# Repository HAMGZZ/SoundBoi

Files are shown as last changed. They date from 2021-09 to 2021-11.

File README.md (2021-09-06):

# SoundBoi
SoundBoi is the codename for a porject which is intended to use with the [BLAT!](https://github.com/hamgzz/BLAT) module for the holden commodored OEM bimodel exhaust. However, it can be extended for use with other cars and valved mufflers. This project originally started when I still had my Holden Barina and wanted an automatic exhaust valve. Over time from trying to write my own CAN transceiver using the teensy line of transceivers and using dodgy rip-off ELM327s with ESP32s, I finally bit the bullet and invested in a few actual ELM327 chips... This is where SoundBoi comes in. SoundBoi is a complete custom solution using the ELM327 chip and an atTiny1614 to communicate with BLAT!. BLAT! is the module the creates the specific PWM and voltages needed to control the OEM Holden mufflers... And yes, all this could be built into one board, but BLAT! came before SoundBoi...

The board follow's a specific set of rules which can be found in the source code.

## Rules
The SoundBoi uses 4 states and a set of rules it follows to determine if the valves should be oppened or closed.
The valve will be open for the first 5 seconds since the car's startup.

### Rules 1 (Default state)
The valve will open if:
 - Speed < 90 AND:
 	- RPM       > 3000
 	- Load      > 50%
 	- Throttle  > 50%
 - Speed > 90 AND:
	- RPM       > 4000
	- Load      > 70%
	- Throttle  > 80%
 - Speed < 5 AND engine is up to temperature.

### Rules 2
The valve will open if:
 - Speed < 90 AND:
	- RPM       > 1900
	- Load      > 30%
	- Throttle  > 30%
 - Speed > 90:
	- Revert back to Rules set 1.
 - Speed < 15 AND engine is up to temperature.

### Rules 3
The valve is always open.

### Rules 4
The valve is always closed.

## PCB

The PCB is meant to be attached to the BLAT! module back-to-back. This is to keep the boards small and modular. The SoundBoi PCB takes it's 5V from the Pololu [regulator](https://www.pololu.com/product/2843) and reads the battery voltage from the 12v coming from the relay on the BLAT! module. Because of the ignition relay, there is no need for low power cutoff on the SoundBoi module, but it might come in future revisions....

### Schematic

<object data="PCB/SoundBoi/SoundBoi.pdf" type="application/pdf" width="700px" height="700px">
    <embed src="PCB/SoundBoi/SoundBoi.pdf">
        <p>This browser does not support PDFs. Please download the PDF to view it: <a href="PCB/SoundBoi/SoundBoi.pdf">Download PDF</a>.</p>
    </embed>
</object>

### 3D Models
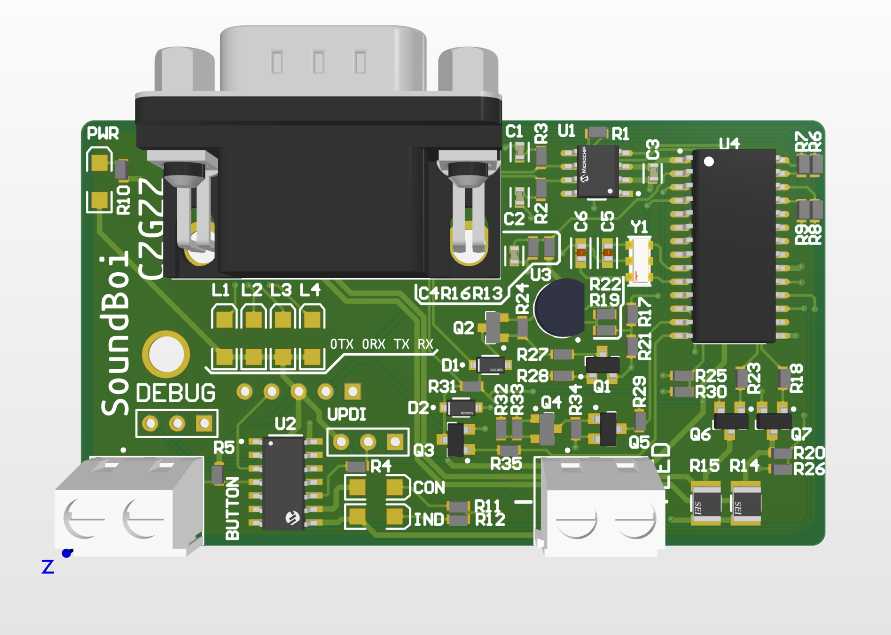
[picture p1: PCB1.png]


### BOM

|Description |Designator |Value  |Manufacturer Part Number 1|Footprint |Quantity|
|---|---|---|---|---|---|
|Female Header, Pitch 5 mm, 1 x 2 Position, Height 10 mm, Tail Length 3.5 mm, Rohs, Bulk |BUTTON, LED | |282836-2 |TECO-282836-2_V |2 |
|CAP CER 560PF 50V X7R 0603 |C1, C2 |560 pF |C0603C561K5RACTU |FP-C0603C-CF-MFG |2 |
|CAP CER 0.1UF 50V X7R 0603 |C3, C4 |0.10 uF|C0603C104K5RACTU |FP-C0603C-CF-MFG |2 |
|Multilayer Ceramic Capacitors 27pF  5% 50V NP0 SMD 0603 |C5, C6 | |C1608NP01H270J080AA |FP-C1608-080-0_1-IPC_A|2 |
|Typical RED, GREEN, YELLOW, AMBER GaAs LED |CON, IND, L1, L2, L3, L4, PWR | | |3.2X1.6X1.1 |7 |
|DIODE GEN PURP 100V 150MA SOD123 |D1, D2 |2pF |1N4148W-13-F |FP-SOD123-MFG |2 |
|Header, 3-Pin |DEBUG, UPDI | | |HDR1X3 |2 |
|Male PCB Connector with Hex Screw WR-DSUB, 10.30 mm, Angled, 9 pins |J1 | |618009231421 |618009231421 |1 |
|Header, 5-Pin |P2 | | |HDR1X5 |1 |
|NPN General Purpose Amplifier, 40 V, 0.2 A, -55 to 150 degC, 3-Pin SOT23, RoHS, Tape and Reel|Q1, Q3, Q5, Q6, Q7 | |MMBT3904 |FAIR-SOT23-3_V |5 |
|General Purpose Transistor, PNP Silicon, 3-Pin SOT-23, Pb-Free, Tape and Reel |Q2, Q4 | |MMBT3906LT1G |ONSC-SOT-23-3-318-08_V|2 |
|Resistor |R1, R4, R27, R28, R29, R35 |4.7K | |J1-0603 |6 |
|Resistor |R2, R3 |100 | |J1-0603 |2 |
|Resistor |R5, R16, R24, R30, R32, R34 |10K | |J1-0603 |6 |
|Resistor |R6, R7, R8, R9, R10, R11, R12, R19, R22|470 | |J1-0603 |9 |
|Resistor |R13, R20, R33 |47K | |J1-0603 |3 |
|510O  5% 0.5W 1210 Thick Film Chip Resistor AEC-Q200 compliant |R14, R15 | |RMCF1210JT510R |FP-RMCF1210-MFG |2 |
|Resistor |R17, R18, R23 |2.2K | |J1-0603 |3 |
|Resistor |R21 |1.8K | |J1-0603 |1 |
|Resistor |R25, R31 |22K | |J1-0603 |2 |
|Resistor |R26 |33K | |J1-0603 |1 |
|IC TRANSCEIVER HALF 1/1 8SOIC |U1 | |MCP2551T-I/SN |FP-C04-057-SN-IPC_B |1 |
|IC MCU 8BIT 16KB FLASH 14SOIC |U2 | |ATTINY1614-SSFR |FP-C04-065-D3X-MFG |1 |
|3-Terminal Adjustable Regulator, 3-pin TO-92 |U3 | |LM317LZG |Z03A |1 |
| |U4 | | |SOIC28 |1 |
|CERAMIC RES 4.0000MHZ 15PF SMD |Y1 | |CSTCR4M00G53-R0 |FP-CSTCR4M00G53-R0-MFG|1 |

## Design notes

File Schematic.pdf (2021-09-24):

# Indicator LEDs

# CAN BUS Transciever

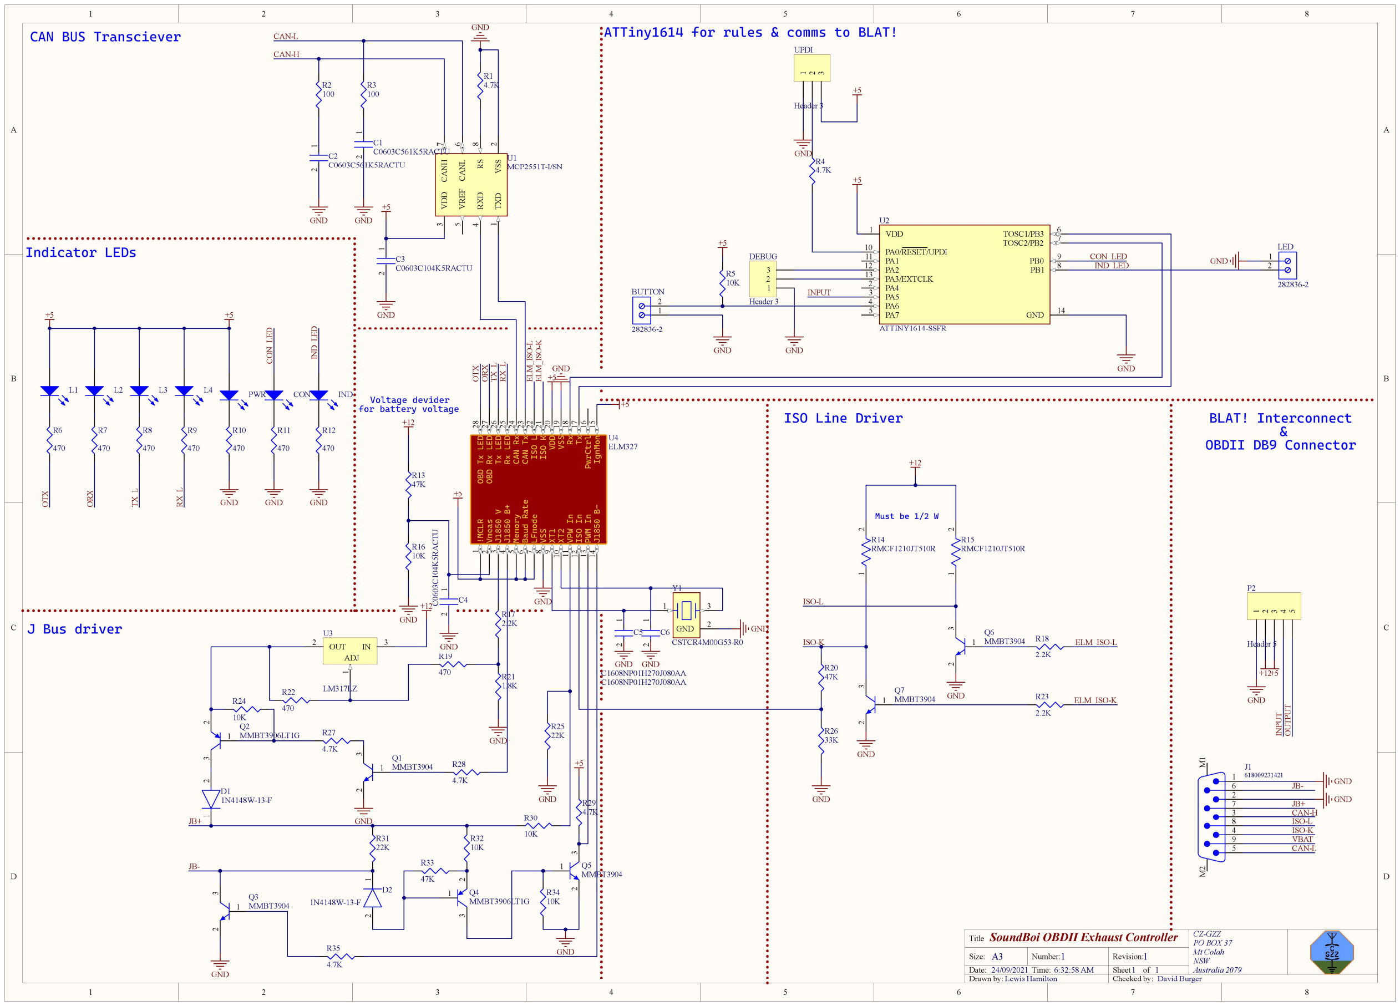
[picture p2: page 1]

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
CZ-GZZ
PO BOX 37
Mt Colah
NSW

### 1 Australia 2079

## SoundBoi OBDII Exhaust Controller

1 1
24/09/2021 6:32:58 AM
Lewis Hamilton

Title

Size: | Number:
Date:
Drawn by:

Revision:
Time: | Sheet | of

A3

Checked by: David Burger

1

2

3

4

5

P2

Header 5

GND

+12+5 INPUT OUTPUT VDD

## 3 CANH

### 7 CANL

### 6 RS

## 8 RXD

### 4 TXD

### 1 VREF

### 5 VSS

2
U1
MCP2551T-I/SN

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
91011121314 1528272625242322212019181716 !MCLR Vmeas J1850 V J1850 B+ Memory Baud Rate LFmode VSS XT1 XT2 VPW In ISO In PWM In J1850 B- IgnMon PwrCtrlRxTx VDD VSS ISO L ISO K Tx LED Rx LED CAN Rx CAN Tx OBD Tx LED OBD Rx LEDU4

ELM327

L1 | L2

470

R7

470

R6

L3 | L4

470

R9

470

R8

+5 | +5 | OTX OTX | ORX ORX | TX_L TX_L | RX_L RX_L

1 2
C3
C0603C104K5RACTU

+5

GND

4.7K

R1

GND
CAN-L

CAN-H

100

R2
100

R3 1 2

C2

C0603C561K5RACTU ¹ ²
C1
C0603C561K5RACTU
GND | GND
1 2 3 | Q1
MMBT3904
1 2 3 | Q3
MMBT3904

1 2 3 Q5

MMBT3904

1 2 3 | Q6
MMBT3904
1 2 3 | Q7
MMBT3904

### 1 ² 3

Q2
MMBT3906LT1G

1 2 3
Q4

MMBT3906LT1G 2 1 D2

1N4148W-13-F ² ¹
D1
1N4148W-13-F

2.2K

R17

470

R19

1.8K

R21

+12

470

R22

10K

R24

4.7K

R27

GND

GND

4.7K

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
4.7K

R35

10K

R34

GND

4.7K

R29

+5

GND

2.2K

R18

2.2K

R23

+12

47K

R20

33K

R26

GND

ELM_ISO-L

ELM_ISO-K ELM_ISO⁻L ELM_ISO⁻K

47K

R13

10K

R16

+12

GND 1 2

# C4 C⁰⁶⁰³C¹⁰⁴K⁵RACTU GND

1 3

GND 2

Y1

CSTCR4M00G53-R0

GND

GND

+5 | 2 1 | C5

C1608NP01H270J080AA ² ¹ C6

C1608NP01H270J080AA

GND GND

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
# 6 M¹ M²

J1
618009231421

VDD 1

PA0/RESET/UPDI 10
PA1 11
PA2 12
PA3/EXTCLK 13
PA4 2
PA5 3
PA6 4
PA7 5
TOSC2/PB2 | 7
TOSC1/PB3 | 6
PB0 | 9
PB1 | 8
GND | 14

U2

ATTINY1614-SSFR

IN | 3 OUT 2 | 1
ADJ

U3

LM317LZ | 1 2 | R14
RMCF1210JT510R | 1 2 | R15

RMCF1210JT510R

GND

GND
CAN-H

CAN-L

ISO-K

JB-

JB+

ISO-L

VBAT

GND

GND

ISO-K

ISO-L

JB-

JB+

INPUT

10K

R5

+5

1

2

BUTTON

282836-2

GND

CON_LED
IND_LED
PWR | CON | IND

470

R10

GND | GND | GND
| 470

R11

470

R12 IND_LED CON_LED

4.7K

R4

GND

+5 ¹

2

3

UPDI

Header 3

+5

GND

1
2

LED

282836-2

GND

+5

GND

+5

1

2

3

DEBUG

Header 3

GND

# J Bus driver

### Voltage devider for battery voltage

# ATTiny1614 for rules & comms to BLAT!

# BLAT! Interconnect

&

# OBDII DB9 Connector

# ISO Line Driver

Must be 1/2 W

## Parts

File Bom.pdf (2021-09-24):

Comment | Description | Designator | Value | Quantity
282836-2 | Female Header, Pitch 5 mm, 1 x 2 Position, Height 10 mm, Tail Length 3.5 mm, Rohs, Bulk | BUTTON, LED | | 2
C0603C561K5RACTU | CAP CER 560PF 50V X7R 0603 | C1, C2 | 560 pF | 2
C0603C104K5RACTU | CAP CER 0.1UF 50V X7R 0603 | C3, C4 | 0.10 μF | 2
C1608NP01H270J080AA Multilayer Ceramic Capacitors 27pF ±5% 50V NP0 SMD 0603 | | C5, C6 | | 2
LED2 | Typical RED, GREEN, YELLOW, AMBER GaAs LED | CON, IND, L1, L2, L3, L4, PWR | | 7
1N4148W-13-F | DIODE GEN PURP 100V 150MA SOD123 | D1, D2 | 2pF | 2
Header 3 | Header, 3-Pin | DEBUG, UPDI | | 2
618009231421 | Male PCB Connector with Hex Screw WR-DSUB, 10.30 mm, Angled, 9 pins | J1 | | 1
Header 5 | Header, 5-Pin | P2 | | 1
MMBT3904 | NPN General Purpose Amplifier, 40 V, 0.2 A, -55 to 150 degC, 3-Pin SOT23, RoHS, Tape and Reel | Q1, Q3, Q5, Q6, Q7 | | 5
MMBT3906LT1G | General Purpose Transistor, PNP Silicon, 3-Pin SOT-23, Pb-Free, Tape and Reel | Q2, Q4 | | 2
Res3 | Resistor | R1, R4, R27, R28, R29, R35 | 4.7K | 6
Res3 | Resistor | R2, R3 | 100 | 2
Res3 | Resistor | R5, R16, R24, R30, R32, R34 | 10K | 6
Res3 | Resistor | R6, R7, R8, R9, R10, R11, R12, R19, R22 | 470 | 9
Res3 | Resistor | R13, R20, R33 | 47K | 3
RMCF1210JT510R | 510Ω ±5% 0.5W 1210 Thick Film Chip Resistor AEC-Q200 compliant | R14, R15 | | 2
Res3 | Resistor | R17, R18, R23 | 2.2K | 3
Res3 | Resistor | R21 | 1.8K | 1
Res3 | Resistor | R25, R31 | 22K | 2
Res3 | Resistor | R26 | 33K | 1
MCP2551T-I/SN | IC TRANSCEIVER HALF 1/1 8SOIC | U1 | | 1
ATTINY1614-SSFR | IC MCU 8BIT 16KB FLASH 14SOIC | U2 | | 1
LM317LZ | 3-Terminal Adjustable Regulator, 3-pin TO-92 | U3 | | 1
ELM327 | | U4 | | 1
CSTCR4M00G53-R0 | CERAMIC RES 4.0000MHZ 15PF SMD | Y1 | | 1

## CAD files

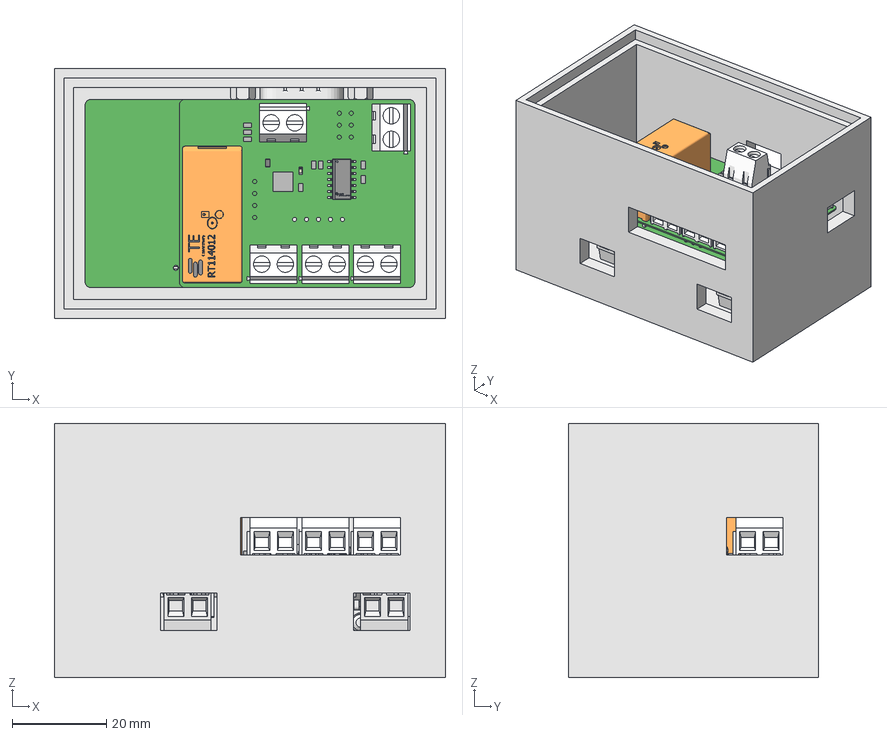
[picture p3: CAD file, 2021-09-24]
BOX/SoundBoi.FCStd
83.0 x 53.0 x 54.0 mm
c-282836-2-h-3d
Base
Pads
Pads001
Pads002
Pads003
Pads004
Pads005
Crystal
Murata
Extruded
IC_BODY
circle
IC_LEG
IC_LEG001
IC_LEG002
IC_LEG003
IC_LEG004
IC_LEG005
IC_LEG006
IC_LEG_MIR8
IC_LEG_MIR009
IC_LEG_MIR010
IC_LEG_MIR011
IC_LEG_MIR012
IC_LEG_MIR013
IC_LEG_MIR014
Microchip_logo
pins
pins001
pins002
pins003
pins004
pins005
pins006
pins007
logo
logo001
logo002
logo003
logo004
logo005
logo006
logo007
logo008
logo009
logo010
Extruded001
Extruded002
Extruded003
Extruded004
Extruded005
Extruded006
Extruded007
Extruded008
Extruded009
Extruded010
Extruded011
Extruded012
Extruded013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

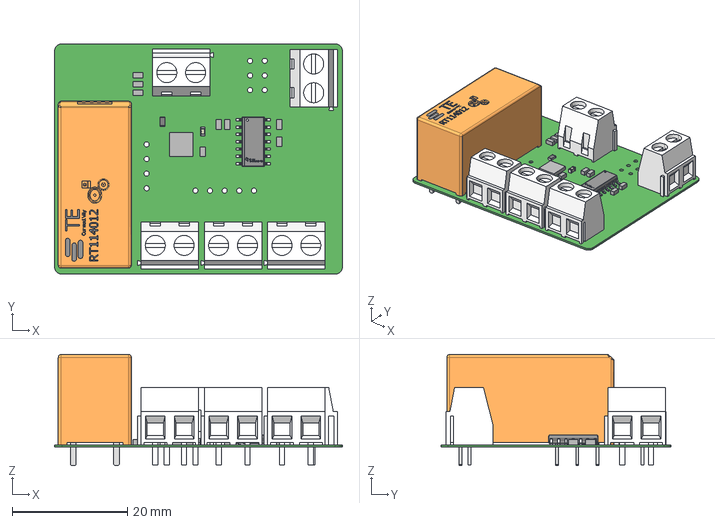
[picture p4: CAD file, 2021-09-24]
BOX/PCB2.step
50.0 x 40.0 x 19.3 mm

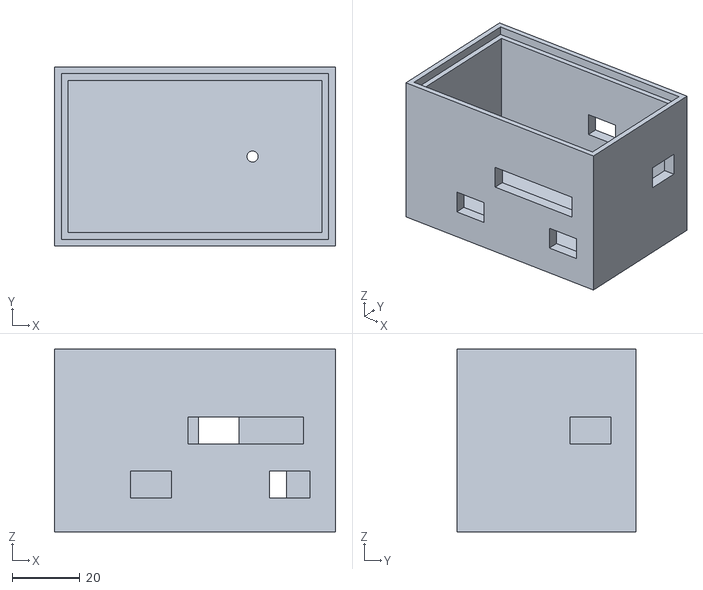
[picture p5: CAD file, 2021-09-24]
BOX/BOX.stl
83.0 x 53.0 x 54.0

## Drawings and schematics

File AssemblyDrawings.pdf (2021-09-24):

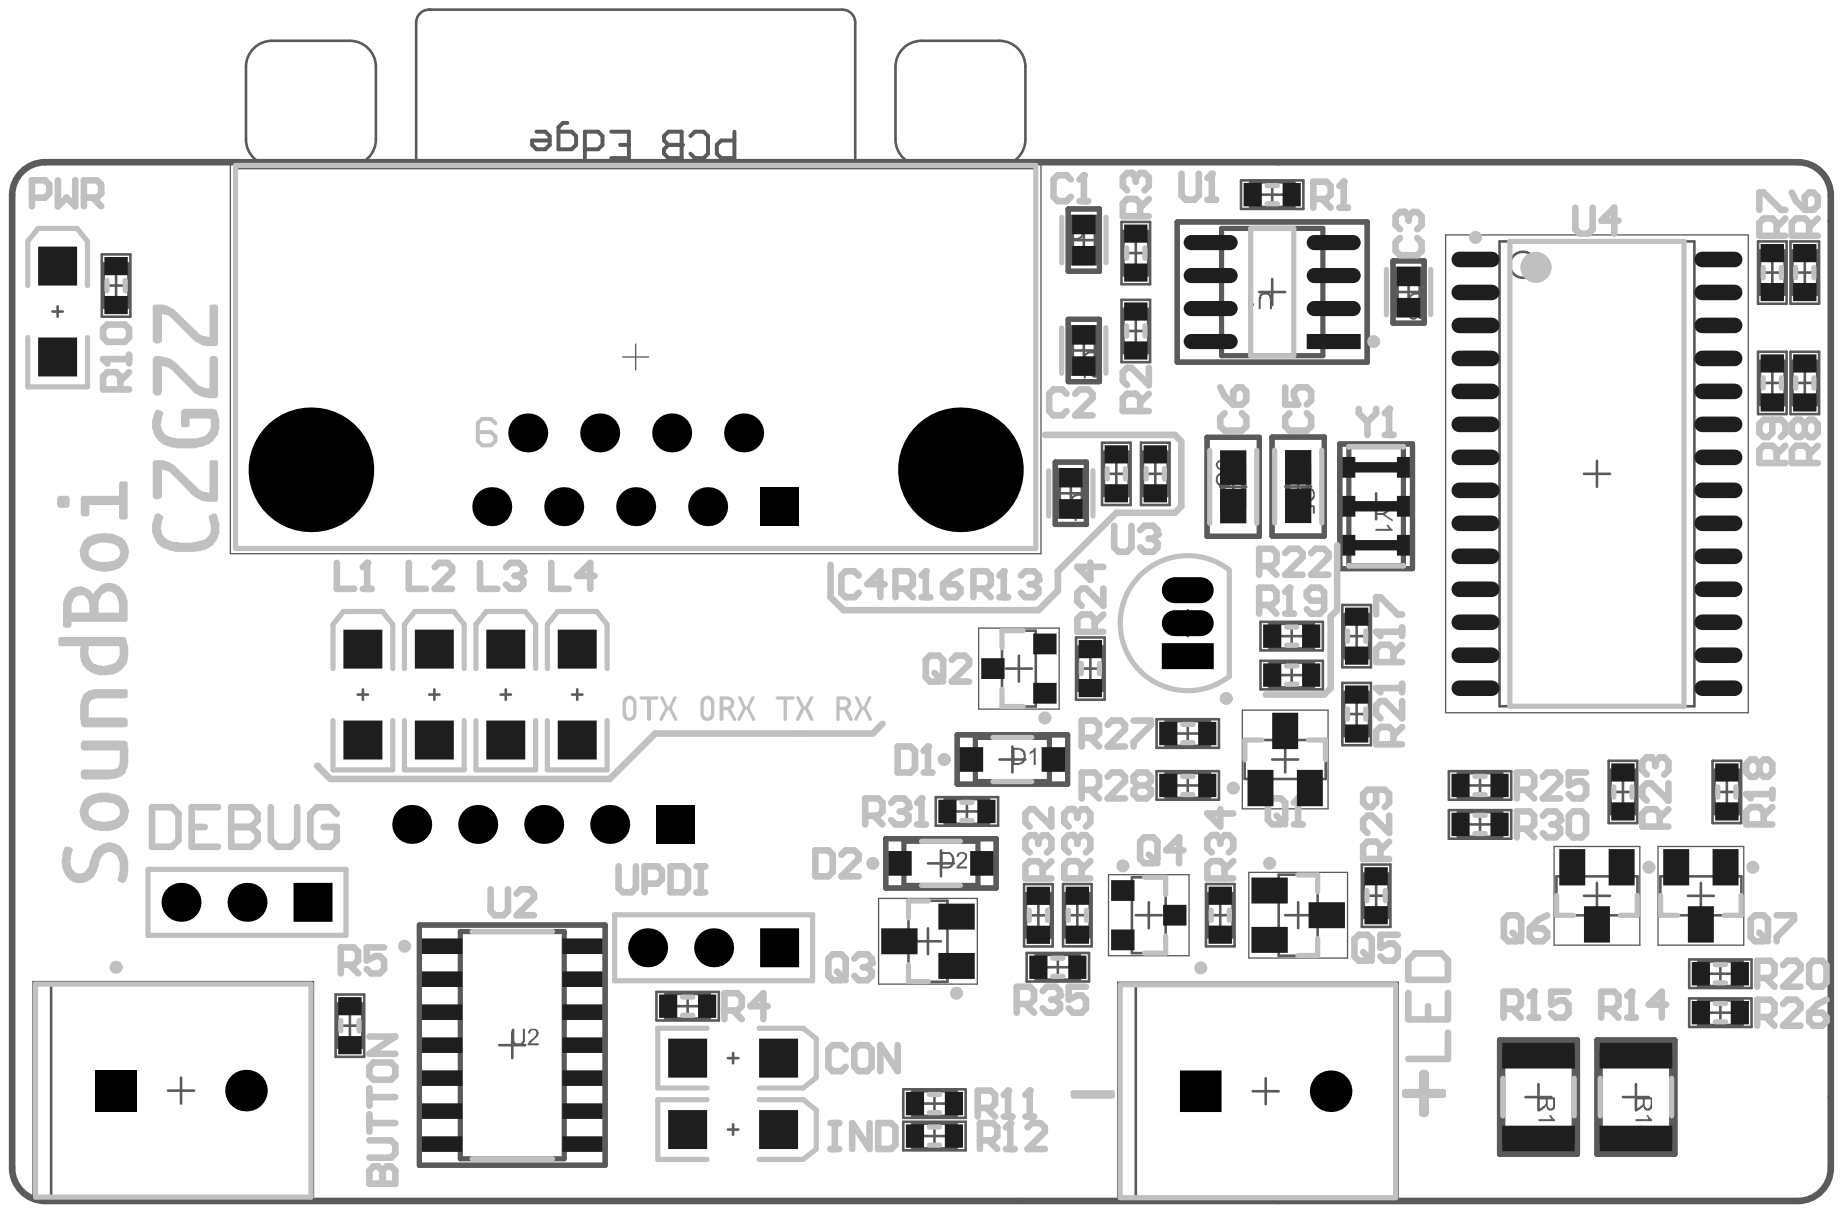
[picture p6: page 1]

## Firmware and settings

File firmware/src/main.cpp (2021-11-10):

/*
 * SoundBoi Exahust controller attiny1614 to interface with BLAT!
 * Version 1.0.1
 */

#include <Arduino.h>
#include <SoftwareSerial.h>
#include "ELMduino.h"

#define VERSION_MAJOR 1
#define VERSION_MINOR 0
#define VERSION_PATCH 1

#define BUTTON                  2           //Pin for button in
#define OUTPUT_PIN              1           //PIN FOR OUTPUT HIGH = OPEN

#define ENGINE_WARMUP_TIME      1           //Number of seconds before valves close after the engine starts

#define IND_LED                 6           //LED pin for displaying what state
#define CON_LED                 7           //Connected to elm327 LED


ELM327 elm;         
SoftwareSerial debug(9, 10);                //Serial line for debugging

int state = 0;                              //State of SoundBoi
int min_state = 0;      
int max_state = 3;                          //GLOBAL VARS for interupt (when connected and not)


//Engine Data Struct
float rpm;
float speed;
float throttle;
float load;
float coolantTemp;
float engineOnTime;


bool rules(bool connected);            //Returns true or false depending on whether the valve should open or close
void blinkLed();  //Blink LED routine for dipiciting what state we are in.
void buttonHandler();                                   //Button ISR
void open();                                            //Open Valve         
void close();                                           //Close Valve



void setup(){}

void loop()
{
    


    Serial.begin(38400);
    debug.begin(9600);

    debug.printf("SoundBoi for BLAT! - Lewis Hamilton September 2021\r\n");
    debug.printf("VERSION: %d.%d.%d\r\n", VERSION_MAJOR, VERSION_MINOR, VERSION_PATCH);
    debug.printf("<<%ld>> Loading variables...", millis());
    

    attachInterrupt(digitalPinToInterrupt(BUTTON), buttonHandler, FALLING);
    
    pinMode(BUTTON, INPUT_PULLUP);
    pinMode(OUTPUT_PIN, OUTPUT);
    pinMode(IND_LED, OUTPUT);
    pinMode(CON_LED, OUTPUT);

    bool connected = false;

    debug.printf("[OK]\r\n");  

    // Open valves for engine start.
    open();

    digitalWrite(IND_LED, HIGH);
    debug.printf("<<%ld>> CONNECTING TO ELM327...", millis());

    if(!elm.begin(Serial,false,1000))
    {
        connected = false;
        debug.printf("[FAIL]\r\n");
        digitalWrite(CON_LED, LOW);
        min_state = 2;
        max_state = 3;
        state = 2;
    }
    else
    {
        connected = true;
        debug.printf("[OK]\r\n");
        digitalWrite(CON_LED, HIGH);
        min_state = 0;
        max_state = 3;
    }
    
    digitalWrite(IND_LED, LOW);

    while(true)
    {
        if(connected)
        {
            float temprpm = elm.rpm();
            float tempspeed = elm.kph();
            float tempthrottle = elm.throttle();
            float tempload = elm.engineLoad();
            float tempcoolantTemp = elm.engineCoolantTemp();
            float tempengineOnTime = elm.runTime();
            if(elm.status == ELM_SUCCESS)
            {
                rpm = temprpm;
                speed = tempspeed;
                throttle = tempthrottle;
                load = tempload;
                coolantTemp = tempcoolantTemp;
                engineOnTime = tempengineOnTime;
                
                debug.printf("<<%lf>> RPM: %lf SPD: %lf THTL: %lf LOAD: %lf TEMP: %lfC ON-TIME: %lfs\r\n", millis(), rpm, speed, throttle, load, coolantTemp, engineOnTime);
            }
            else
            {
                debug.printf("<<%lf>> ELM FAIL!", millis());
            }
        }
        
        if(rules(connected))
        {
            open();
        }
        else
        {
            close();
        }

        blinkLed();
    }
}

bool rules(bool connected)
{
    bool openValve = true;
    if(state == 0 && engineOnTime > ENGINE_WARMUP_TIME)
    {
        if((rpm > 3000 || throttle > 70) && speed < 80)
            openValve = true;
        else if((rpm >  4000 || throttle > 80) && speed >= 80)
            openValve = true;
        else
            openValve = false;
    }

    else if(state == 1 && engineOnTime > ENGINE_WARMUP_TIME)
    {
        if((rpm > 2500 || load > 80 || throttle > 50) && speed < 90)
            openValve = true;
        else if(speed < 40 && coolantTemp > 50)
            openValve = true;
        else if(speed >= 110)
        {
            state = 0;
        }
        else
            openValve = false;
    }

    else if(state == 2)
    {
        openValve = false;
    }

    else if(state == 3)
    {
        openValve = true;
    }

    if(((rpm < 50 || engineOnTime < ENGINE_WARMUP_TIME) && connected) && state != 2)
    {
        if(coolantTemp > 50)
        {
            delay(10000);
        }
        openValve = true;
    }


    return openValve;
}

void open()
{
    debug.printf("<<%ld>> Opening valves!\r\n", millis());
    digitalWrite(OUTPUT_PIN, HIGH);
    delay(1000);
}

void close()
{
    debug.printf("<<%ld>> Closing valves!\r\n", millis());
    digitalWrite(OUTPUT_PIN, LOW);
    delay(1000);
}

void blinkLed()
{
    if(state == 0)
    {
        analogWrite(IND_LED, 10);
        delay(200);
        digitalWrite(IND_LED, LOW);
    }
    else if(state == 1)
    {
        analogWrite(IND_LED, 10);
        delay(10);
        digitalWrite(IND_LED, LOW);
    }
    else if(state == 2)
    {
        digitalWrite(IND_LED, LOW);
    }
    else if(state == 3)
    {
        analogWrite(IND_LED, 10);
    }
}


void buttonHandler()
{
  static unsigned long last_interrupt_time = 0;
  unsigned long interrupt_time = millis();
  // If interrupts come faster than 200ms, assume it's a bounce and ignore
  if (interrupt_time - last_interrupt_time > 200) 
  {
      state++;
      if(state > max_state)
      {
          state = 0;
      }
      if(state < min_state)
      {
          state = min_state;
      }
  }
  debug.printf("<<%ld>> Button pushed >> STATE %d", millis(), state);
  last_interrupt_time = interrupt_time;
}

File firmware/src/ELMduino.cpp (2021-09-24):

#include "ELMduino.h"




/*
 bool ELM327::begin(Stream &stream, const bool& debug, const uint16_t& timeout, const char& protocol, const uint16_t& payloadLen, const byte& dataTimeout)

 Description:
 ------------
  * Constructor for the ELM327 Class; initializes ELM327

 Inputs:
 -------
  * Stream &stream      - Reference to //Serial port connected to ELM327
  * bool debug          - Specify whether or not to print debug statements to "//Serial"
  * uint16_t timeout    - Time in ms to wait for a query response
  * char protocol       - Protocol ID to specify the ELM327 to communicate with the ECU over
  * uint16_t payloadLen - Maximum number of bytes expected to be returned by the ELM327 after a query
  * byte dataTimeout    - Number of ms to wait after receiving data before the ELM327 will
						  return the data - see https://www.elmelectronics.com/help/obd/tips/#UnderstandingOBD
 Return:
 -------
  * bool - Whether or not the ELM327 was propperly
  initialized
*/
bool ELM327::begin(Stream &stream, const bool& debug, const uint16_t& timeout, const char& protocol, const uint16_t& payloadLen, const byte& dataTimeout)
{
	elm_port    = &stream;
	PAYLOAD_LEN = payloadLen;
	debugMode   = debug;
	timeout_ms  = timeout;

	payload = (char*)malloc(PAYLOAD_LEN + 1); // allow for terminating '\0'

	if (!elm_port)
		return false;

	// try to connect
	if (!initializeELM(protocol, dataTimeout))
		return false;
  
	return true;
}




/*
 bool ELM327::initializeELM(const char& protocol, const byte& dataTimeout)

 Description:
 ------------
  * Initializes ELM327

 Inputs:
 -------
  * char protocol    - Protocol ID to specify the ELM327 to communicate with the ECU over
  * byte dataTimeout - Number of ms to wait after receiving data before the ELM327 will
                       return the data - see https://www.elmelectronics.com/help/obd/tips/#UnderstandingOBD

 Return:
 -------
  * bool - Whether or not the ELM327 was propperly initialized

 Notes:
 ------
  * Protocol - Description
  * 0        - Automatic
  * 1        - SAE J1850 PWM (41.6 kbaud)
  * 2        - SAE J1850 PWM (10.4 kbaud)
  * 3        - ISO 9141-2 (5 baud init)
  * 4        - ISO 14230-4 KWP (5 baud init)
  * 5        - ISO 14230-4 KWP (fast init)
  * 6        - ISO 15765-4 CAN (11 bit ID, 500 kbaud)
  * 7        - ISO 15765-4 CAN (29 bit ID, 500 kbaud)
  * 8        - ISO 15765-4 CAN (11 bit ID, 250 kbaud)
  * 9        - ISO 15765-4 CAN (29 bit ID, 250 kbaud)
  * A        - SAE J1939 CAN (29 bit ID, 250* kbaud)
  * B        - User1 CAN (11* bit ID, 125* kbaud)
  * C        - User2 CAN (11* bit ID, 50* kbaud)

  * --> *user adjustable
*/
bool ELM327::initializeELM(const char& protocol, const byte& dataTimeout)
{
	char command[10] = { '\0' };
	connected = false;

	sendCommand(SET_ALL_TO_DEFAULTS);
	delay(100);

	sendCommand(RESET_ALL);
	delay(100);

	sendCommand(ECHO_OFF);
	delay(100);

	sendCommand(PRINTING_SPACES_OFF);
	delay(100);

	sendCommand(ALLOW_LONG_MESSAGES);
	delay(100);

	// Set data timeout
	sprintf(command, SET_TIMEOUT_TO_H_X_4MS, dataTimeout / 4);
	sendCommand(command);
	delay(100);

	// Set protocol
	sprintf(command, TRY_PROT_H_AUTO_SEARCH, protocol);

	if (sendCommand(command) == ELM_SUCCESS)
	{
		if (strstr(payload, "OK") != NULL)
		{
			connected = true;
			return connected;
		}
	}
	// Set protocol and save
	sprintf(command, SET_PROTOCOL_TO_H_SAVE, protocol);

	if (sendCommand(command) == ELM_SUCCESS)
		if (strstr(payload, "OK") != NULL)
			connected = true;

	if (debugMode)
	{
		//Serial.print(F("Setting protocol via "));
		//Serial.print(SET_PROTOCOL_TO_H_SAVE);
		//Serial.println(F(" did not work"));
	}

	return connected;
}




/*
 void ELM327::formatQueryArray(uint8_t service, uint16_t pid)

 Description:
 ------------
  * Creates a query stack to be sent to ELM327

 Inputs:
 -------
  * uint16_t service - Service number of the queried PID
  * uint32_t pid     - PID number of the queried PID

 Return:
 -------
  * void
*/
void ELM327::formatQueryArray(uint8_t service, uint16_t pid)
{
	if (debugMode)
	{
		//Serial.print(F("Service: "));
		//Serial.println(service);
		//Serial.print(F("PID: "));
		//Serial.println(pid);
	}

	query[0] = ((service >> 4) & 0xF) + '0';
	query[1] = (service & 0xF) + '0';

	// determine PID length (standard queries have 16-bit PIDs,
	// but some custom queries have PIDs with 32-bit values)
	if (pid & 0xFF00)
	{
		if (debugMode)
			//Serial.println(F("Long query detected"));

		longQuery = true;

		query[2] = ((pid >> 12) & 0xF) + '0';
		query[3] = ((pid >> 8) & 0xF) + '0';
		query[4] = ((pid >> 4) & 0xF) + '0';
		query[5] = (pid & 0xF) + '0';

		upper(query, 6);
	}
	else
	{
		if (debugMode)
			//Serial.println(F("Normal length query detected"));

		longQuery = false;

		query[2] = ((pid >> 4) & 0xF) + '0';
		query[3] = (pid & 0xF) + '0';
		query[4] = '\0';
		query[5] = '\0';

		upper(query, 4);
	}

	if (debugMode)
	{
		//Serial.print(F("Query string: "));
		//Serial.println(query);
	}
}




/*
 void ELM327::upper(char string[], uint8_t buflen)

 Description:
 ------------
  * Converts all elements of char array string[] to
  uppercase ascii

 Inputs:
 -------
  * uint8_t string[] - Char array
  * uint8_t buflen   - Length of char array

 Return:
 -------
  * void
*/
void ELM327::upper(char string[], uint8_t buflen)
{
	for (uint8_t i = 0; i < buflen; i++)
	{
		if (string[i] > 'Z')
			string[i] -= 32;
		else if ((string[i] > '9') && (string[i] < 'A'))
			string[i] += 7;
	}
}




/*
 bool ELM327::timeout()

 Description:
 ------------
  * Determines if a time-out has occurred

 Inputs:
 -------
  * void

 Return:
 -------
  * bool - whether or not a time-out has occurred
*/
bool ELM327::timeout()
{
	currentTime = millis();
	if ((currentTime - previousTime) >= timeout_ms)
		return true;
	return false;
}




/*
 uint8_t ELM327::ctoi(uint8_t value)

 Description:
 ------------
  * converts a decimal or hex char to an int

 Inputs:
 -------
  * uint8_t value - char to be converted

 Return:
 -------
  * uint8_t - int value of parameter "value"
*/
uint8_t ELM327::ctoi(uint8_t value)
{
	if (value >= 'A')
		return value - 'A' + 10;
	else
		return value - '0';
}
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

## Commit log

2021-09-06 Added PCB files
    [ELM327.PcbLib, ELM327.SchLib, Main.SchDoc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]
2021-09-06 Added schematic
    [Main.SchDoc]
2021-09-06 Added pcb image
    [Main.SchDoc, SoundBoi.PrjPcb]
2021-09-06 Added BOM
2021-11-10 Valve is only open when Stopped
2021-11-10 added more stuff
    [Main.SchDoc]
